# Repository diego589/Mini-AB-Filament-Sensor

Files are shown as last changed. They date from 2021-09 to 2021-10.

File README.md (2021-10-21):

# Filament sensor for Dragon Mini AB
I wanted to create an invisible filament sensor inside the toolhead to check if the filament runs out or if there is a clog in the extruder gears. Tested on Dragon normal flow, not tested on Dragonfly, but it should work.

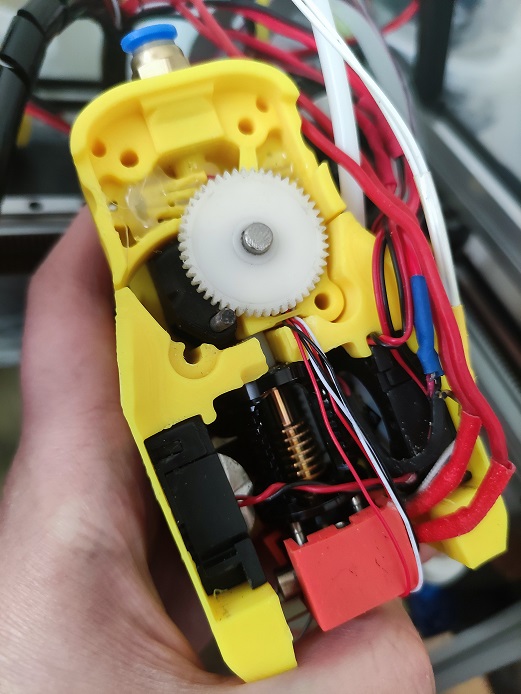
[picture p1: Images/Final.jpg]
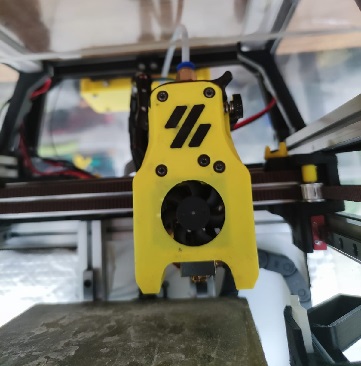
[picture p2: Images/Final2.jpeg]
  

https://user-images.githubusercontent.com/67475249/138114734-22fbd80a-b481-46d0-a8a0-9267f2467829.mp4

# BOM
## For both (before and after the extruder's gears)
- 1x M6 Nut
- [1x Pneumatic Fittings PC4 - M6](https://www.aliexpress.com/item/32844004441.html)
- [2x digital hall sensor](http://aliexpress.com/item/32312432947.html), it doesn't matter if it's [latching or not](https://maker.pro/arduino/tutorial/how-to-use-a-hall-effect-sensor-with-arduino). I'm using U18
- [7x 4mm ball bearings](http://www.aliexpress.com/item/1005002383413769.html)
- [4x 5mm x 3mm Round Neodymium Magnets](https://www.aliexpress.com/item/1005002226737225.html)
- 2x 10k ohm resistor
- [Thin wires, 32 AWG recommended](https://www.aliexpress.com/item/32882386535.html)

## BOM If you only want a sensor before the gears:
- 1x M6 Nut
- 1x Pneumatic Fittings PC4 - M6
- 1x Digital hall sensor
- 1x ball bearing
- 2x Magnets
- 1x resistor
- Thin wires

## BOM If you only want a sensor after the gears:
- 1x M6 Nut
- 1x Pneumatic Fittings PC4 - M6
- 1x Digital hall sensor
- 6x ball bearings
- 2x Magnets
- 1x resistor
- Thin wires

## Tools
- Multimeter

# Printed parts
- _[a]FS_Mid_Body.stl_ - Needed
- Recommended to print 2 copies of every hall sensor holder
- _[a]FS_Cowling_Dragon.stl_ - Not needed at all, but print it if you don't want to sand it down (step 13)

# Assembly
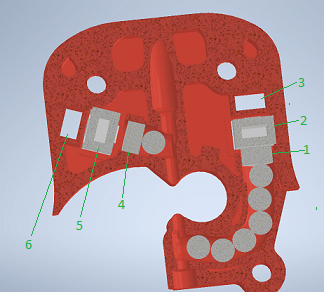
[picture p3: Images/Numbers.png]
f2


0. Insert a M6 nut into the hole and then tighten the pneumatic fitting
1. Insert 6 balls in **1**
2. Insert magnet in **1**
3. Make sure that magnet is around 2mm down the tunnel, if not, then push it using filament or something similar
4. Test your clearances by inserting filament, when there is no filament the magnet should be 2mm down the tunnel and when the filament is loaded, the magnet should raise up about 2mm

https://user-images.githubusercontent.com/67475249/134376186-ed08a0d5-9afd-461a-8bc8-b10c32558bfe.mp4

6. Insert a magnet in **3**, it should repel the magnet in **1**. If you inserted it in the wrong orientation use an 1.5 or 2mm drill bit to remove it out of the hole
7. Prepare hall sensor, solder resistor at no less than 10 cm from the sensor

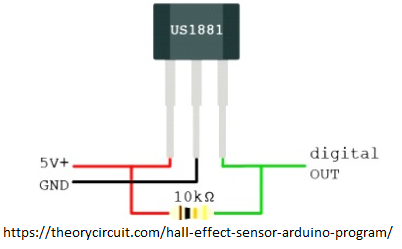
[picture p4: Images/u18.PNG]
f5

 
8. Test your circuit, move the hall sensor towards each magnets and check with a multimeter between GND and OUT, it should read 5v next to one and 0v next to the other
9. Insert the hall sensor in _[a]HallSensorHolder145-145.stl_, then insert the holder with the sensor in **2** (small face of sensor pointing towards **3**). **DO NOT** force it yet
11. Load and unload filament and check with a multimeter if there is any variation, if the voltage doesn't change, rotate hall sensor and repeat
   * If everything is working, push the hallsensor holder in place
   * If it's not working, remove it and try with a different sensor holder, then repeat
12. For the sensor that goes before the gears follow the same instructions but use just 1 ball bearing instead
13. Bend the sensor pins until they are below the highlighted part (image below)

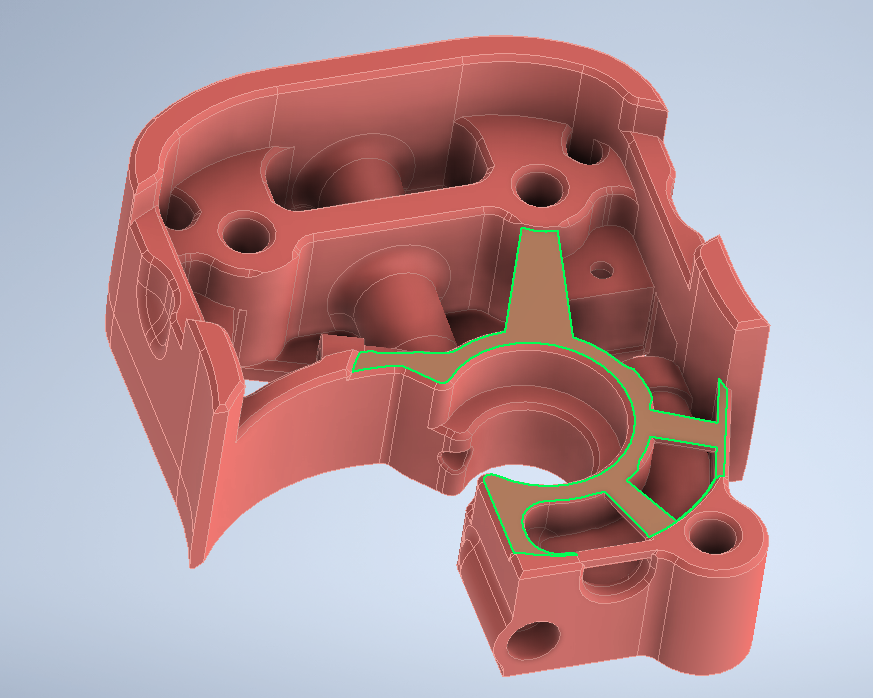
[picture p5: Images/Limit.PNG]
f6


13. Route your cable following the path as shown in the image below. If you didn't print _[a]FS_Cowling_Dragon.stl_ you have to sand a path down yourself (black circle in image below)

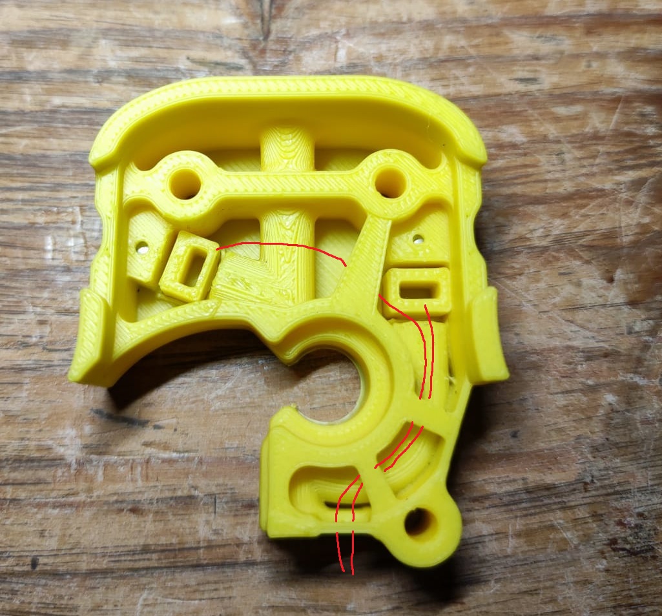
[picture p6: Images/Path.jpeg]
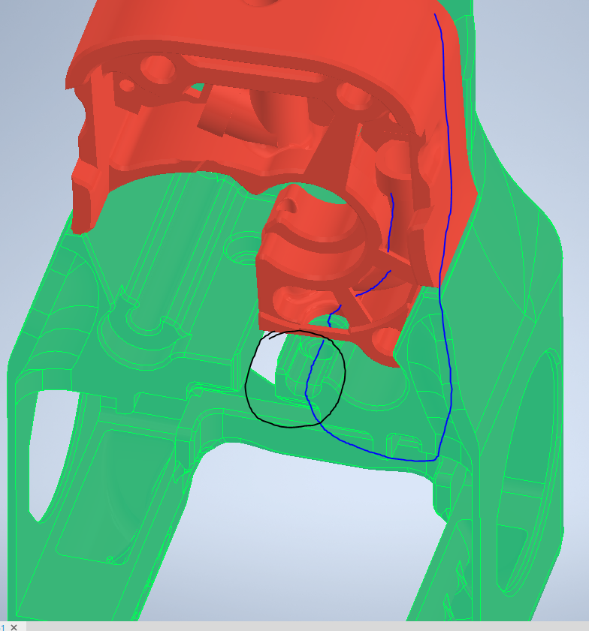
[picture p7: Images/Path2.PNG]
 

14. Choose any available pin on your board. In this case I am using RX2 and TX2 because they are right next to GND and +5v. See _TestCode.txt_
 
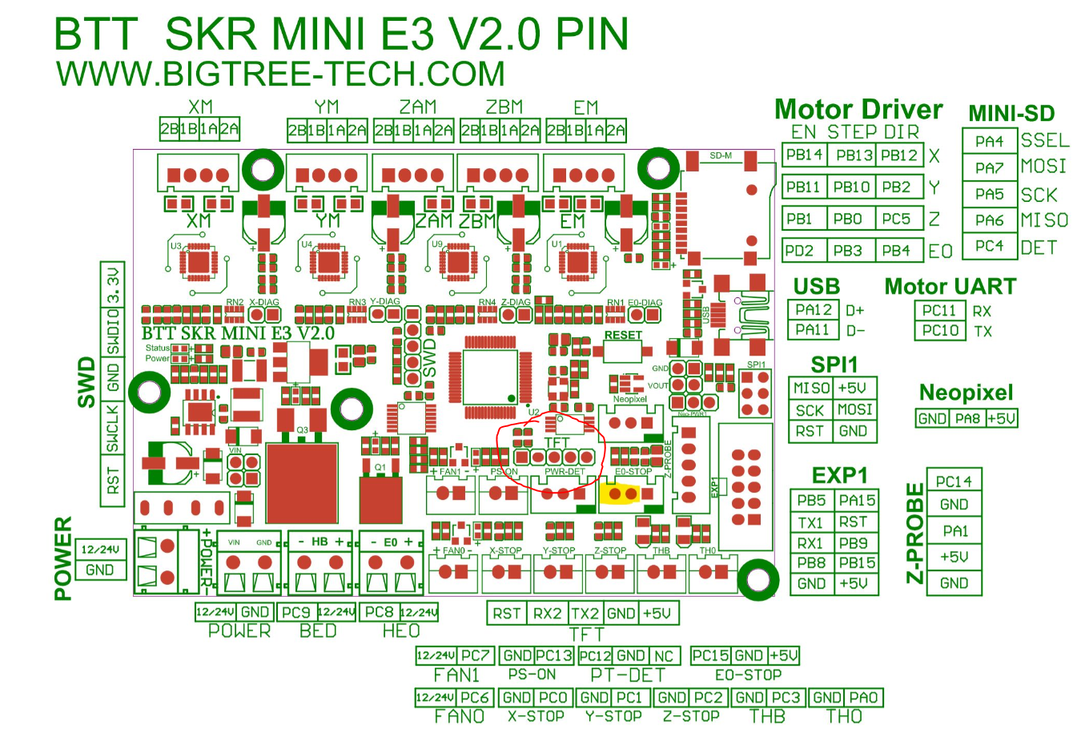
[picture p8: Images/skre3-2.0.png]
f9


# Photos
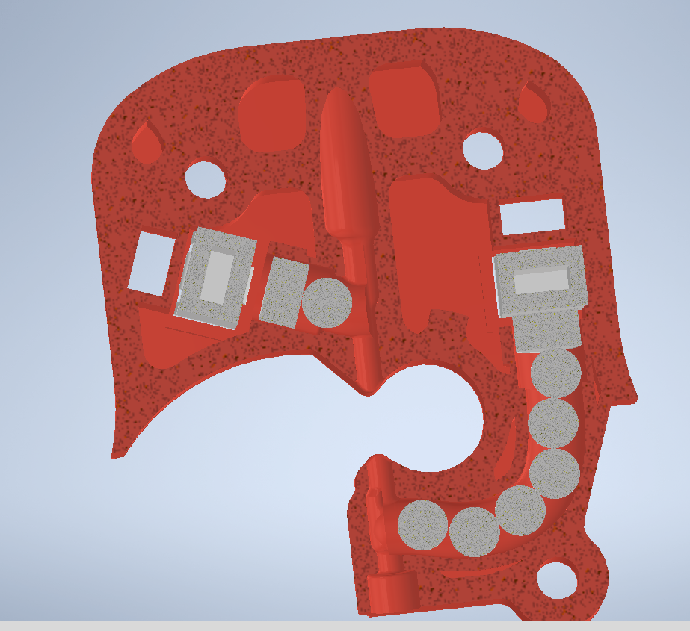
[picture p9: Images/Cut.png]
 
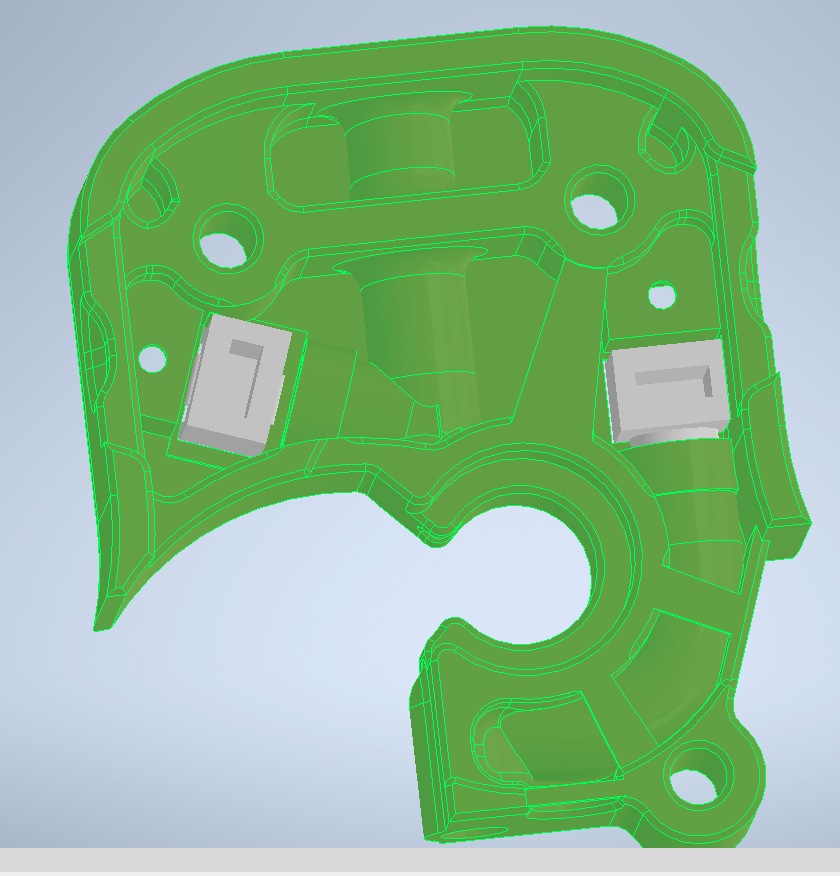
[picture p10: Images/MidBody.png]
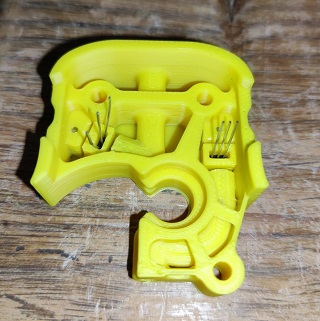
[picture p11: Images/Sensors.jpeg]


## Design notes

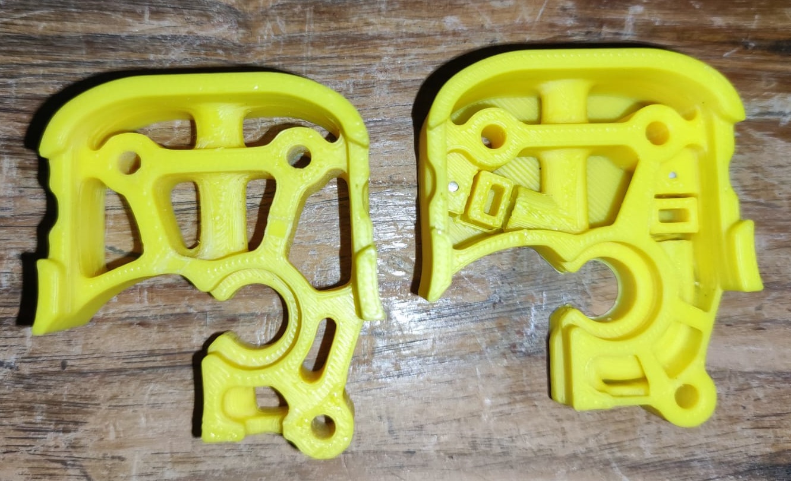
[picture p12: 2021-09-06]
Images/Comparison.jpeg

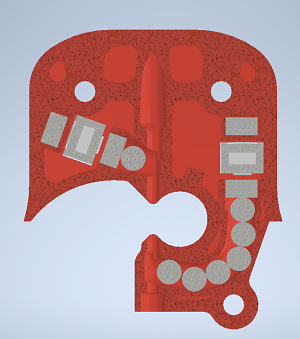
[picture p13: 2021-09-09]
Images/Load.png

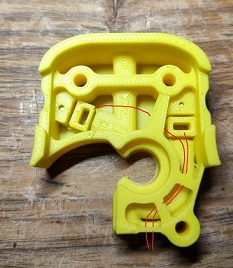
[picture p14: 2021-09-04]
Images/CablePath.jpeg

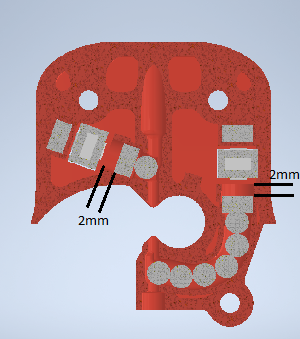
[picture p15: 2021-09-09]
Images/Unload.png

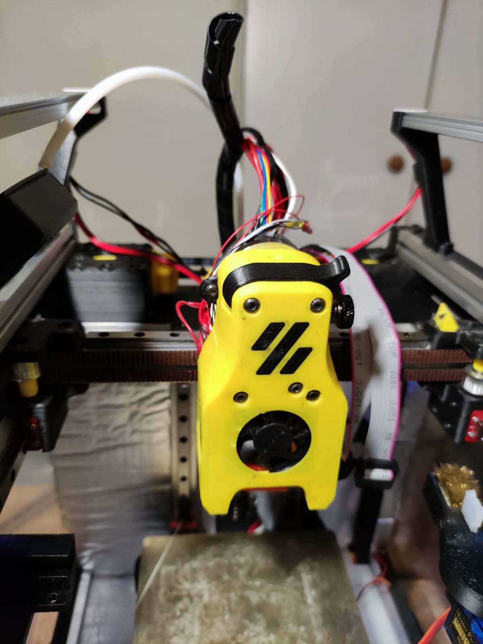
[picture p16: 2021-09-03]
Images/Final.jpeg

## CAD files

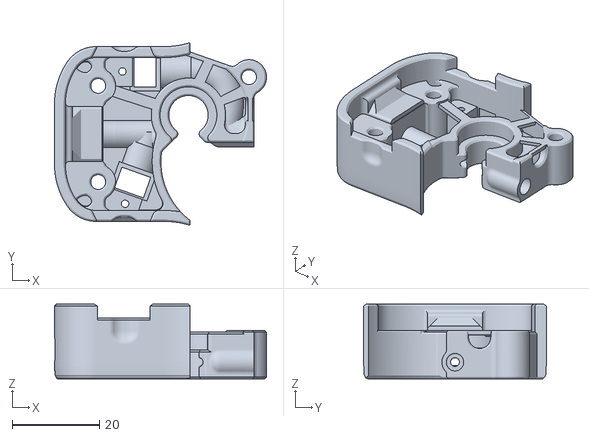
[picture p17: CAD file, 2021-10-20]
[a]Mid_Body - PC4-M6 - 6x3 magnets.stl
48.5 x 41.8 x 17.0

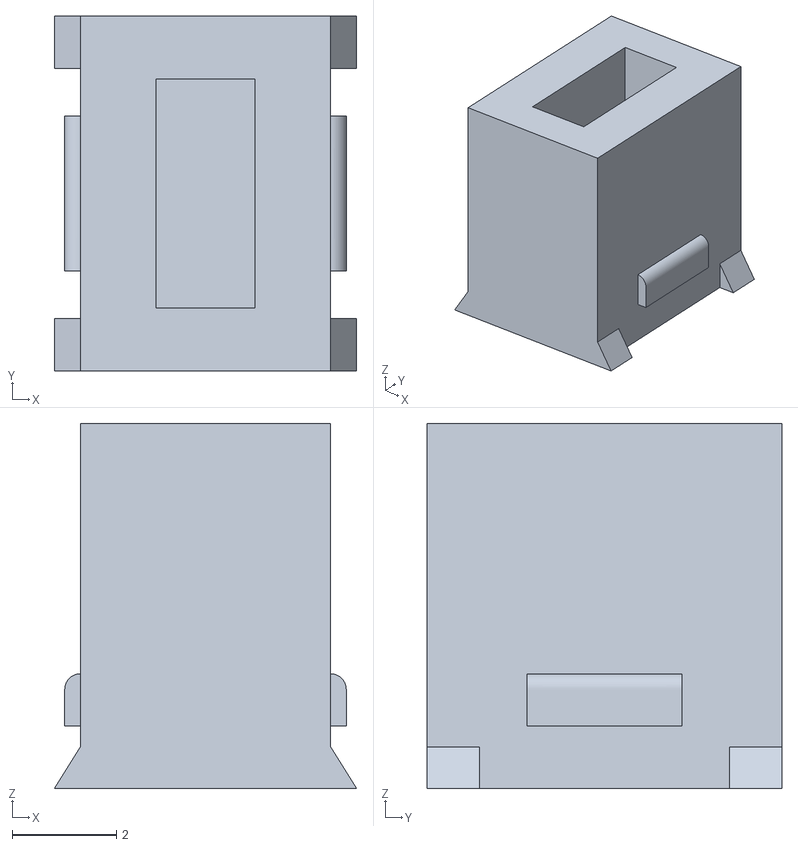
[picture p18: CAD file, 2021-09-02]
[a]HallSensorHolder145-145.stl
5.80 x 6.80 x 7.00

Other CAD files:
CAD/Mid_Body - PC4-M6.stp
[a]HallSensorHolder80-210.stl
[a]HallSensorHolder100-190.stl
[a]HallSensorHolder40-250.stl

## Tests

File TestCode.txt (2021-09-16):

[respond]

[filament_switch_sensor Before]
pause_on_runout: False
runout_gcode: RESPOND MSG="Before - No filament"
event_delay: 0.1
switch_pin: ^!PA2 ;TX2 - Remove "!" to reverse polarity

[filament_switch_sensor After]
pause_on_runout: False
runout_gcode: RESPOND MSG="After - No filament"
event_delay: 0.1
switch_pin: ^!PA3 ;RX2 - Remove "!" to reverse polarity

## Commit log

2021-09-02 Filament sensor for Mini AB
    V0.9 - It's working, but instructions not included.
    [2 Sensores.iam, Ball 4mm.ipt, Brazo Sensor.ipt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]
2021-09-03 Remove useless files
    Remove .ipt and .iam files and add some pictures.
    [2 Sensores.iam, Ball 4mm.ipt, Brazo Sensor.ipt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]
2021-09-03 Rename files
    [Hall Sensor Holder 100-190.stl, Hall Sensor Holder 145-145.stl, Hall Sensor Holder 40-250.stl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]
2021-09-04 Fixed .stl
2021-09-04 Fixed filenames
    [Hall Sensor Holder 100-190.stl, Hall Sensor Holder 145-145.stl, Hall Sensor Holder 40-250.stl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]
2021-09-22 CAD
    CAD for bowden fitting and video
    [Mid_Body - bowden fitting.ipt, Mid_Body - bowden fitting.stp, Mid_Body - only after.stp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]
2021-09-22 Create Mid_Body - bowden fitting - Not Tested.stl
    [Mid_Body - bowden fitting - Not Tested.stl]
2021-09-24 New bowden fitting
    [Mid_Body - Test Bowden Fitting.stp, Mid_Body - bowden fitting.ipt, Mid_Body - bowden fitting.stp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]
2021-09-24 Small fix
    [Mid_Body - Test Bowden Fitting.stp]
2021-10-20 CAD Updated
    CAD files using 6x3 mm magnets
    [Mid_Body - PC4-M6.stp, Mid_Body - Test Bowden Fitting.stp, Mid_Body - only after.stp]
2021-10-20 BOM Updated
